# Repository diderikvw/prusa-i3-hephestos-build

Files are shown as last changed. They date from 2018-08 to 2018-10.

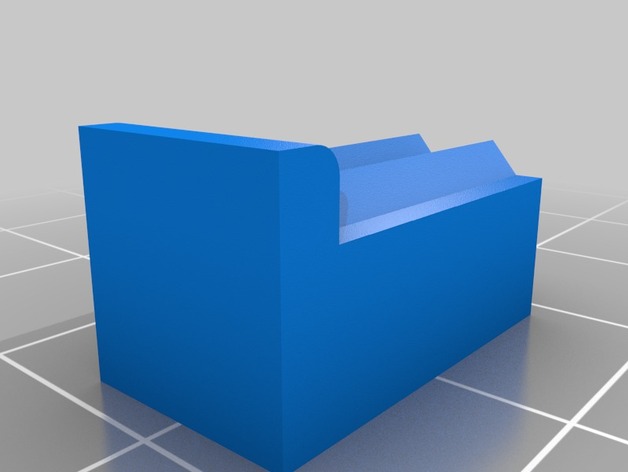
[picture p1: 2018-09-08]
3D Printable Parts/Thingiverse/By pixelmagic (thing 1411994)/images/da518802a75f78a3230417619e0c3546_preview_featured.jpg

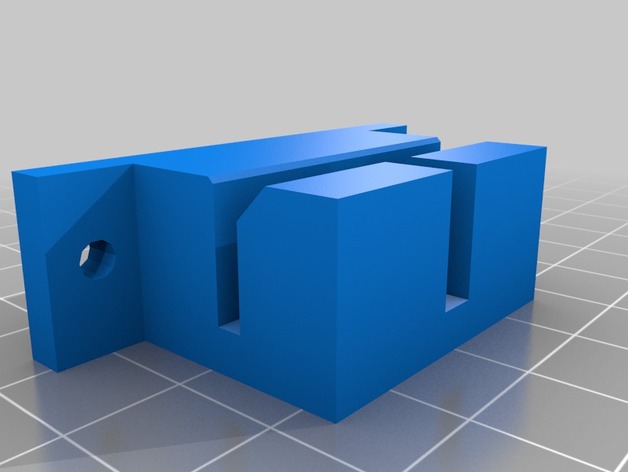
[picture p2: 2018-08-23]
3D Printable Parts/Thingiverse/By bqLabs (thing 371842)/images/EjeY_sujeta_correa_preview_featured.jpg

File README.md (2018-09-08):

# prusa-i3-hephestos-build
Repo to store stuff while building the 3D Printer Prusa i3 Hephestos

Information:
https://reprap.org/wiki/Prusa_i3_Hephestos

3D Printable parts:
Original Spanish: https://www.thingiverse.com/thing:371842
PLA
Infill 20%
0.1mm

English STL only: https://www.thingiverse.com/thing:1411994/

https://github.com/bq/prusa-i3-hephestos/tree/master/stl

https://www.bq.com/en/support/prusa/support-sheet

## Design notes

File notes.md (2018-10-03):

# Notes

## BOM

### Smooth rods
8mm
2 x 37 cm
2 x 34 cm
2 x 32 cm
total: 206 cm

reprapworld.nl 3 x 100 cm = EUR 12
aliexpress more expensive

### Flexible coupling
2x 5/5mm

reprapworld EUR 4 a piece = EUR 8
aliexpress EUR 1 a piece + EUR 4 shipping 12-15 days = EUR 5

### axial ball bearing B623ZZ
2x

reprapworld EUR 0,75 a piece

### GT2 pulley
20 teeth
diameter?
2x

reprapworld EUR 4 a piece = EUR 8
aliexpress EUR 0,50 + EUR 4 schipping 12-15 days = EUR 5

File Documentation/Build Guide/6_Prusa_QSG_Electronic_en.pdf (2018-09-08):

6

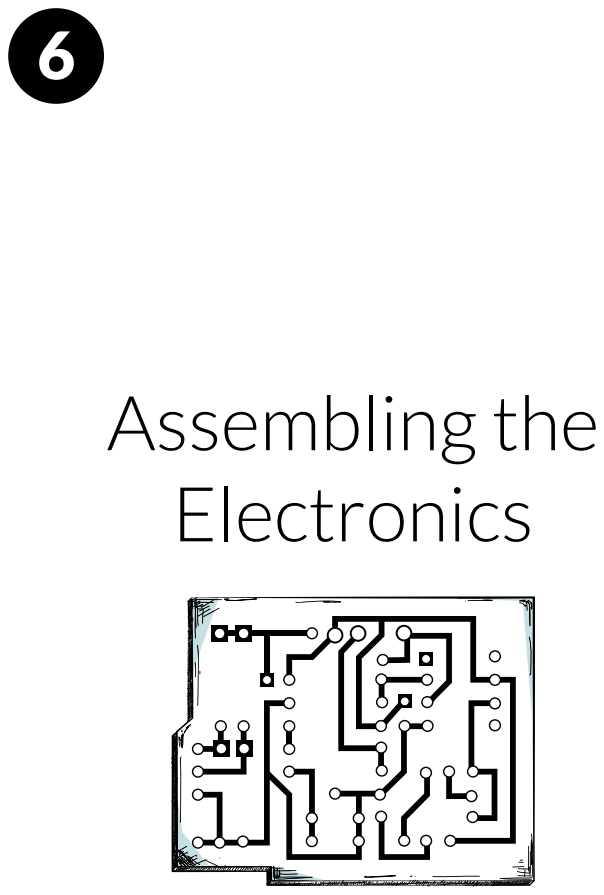
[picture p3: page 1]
Assembling the Electronics

### 1 x Ramps 1.4 (with 4 x Stepstick Drivers A4988 mounted) 3 x End-stop 1 x LCD Control Panel 1 x USB cable, type B, 1.8 metres 4 x Cable motor Nema 17 2 x Cable end-stop 40 cm 1 x Cable end-stop 85 cm 4 x Motor Nema 17 1 x Kit of cables for the extruder: Four-strand cable for Nema

17 bipolar step motor (2.5A 1.8 deg/step) with connector JST XHP-6 and 4-pin female connector + two-strand cable for thermistor of the extruder with 2-pin female connector
+ Cable for fan clamped to with nipple terminal + Cable blower clamped to with nipple terminal + Cable for cartridge heater clamped to with nipple terminal.

### 1 x Cable prepared for power supply (150 mm of flexible, two-

strand, bicolour cable with cross section of 1.5 mm² + Jack Adapter/ connector)

1 x 220 AC 12 DC 100W power supply 1 x Power supply/Network cable 1 x LCD Hinge printed part 1 x Ramp Bracket printed part 4 x Screw M3 x 10 - DIN-912 class 8.8 black 2 x Screw M3 x 12 - DIN-912 class 8.8 black 2 x Screw M3 x 16 - DIN-912 class 8.8 black 4 x Screw M3 x 20 - DIN-912 class 8.8 black 2 x Nut M3 - DIN 934 class 8 black 1 x Thermo-retractable tube of Ø2.5 x 500 mm 11 x Black strap 100 x 2.5 mm 1 x Fan 50 x 50 mm 2 x Igus Cable-carrier chain (25 and 27 links)

# List of components for the Electronics

1

# Installing the RAMPS 1.4

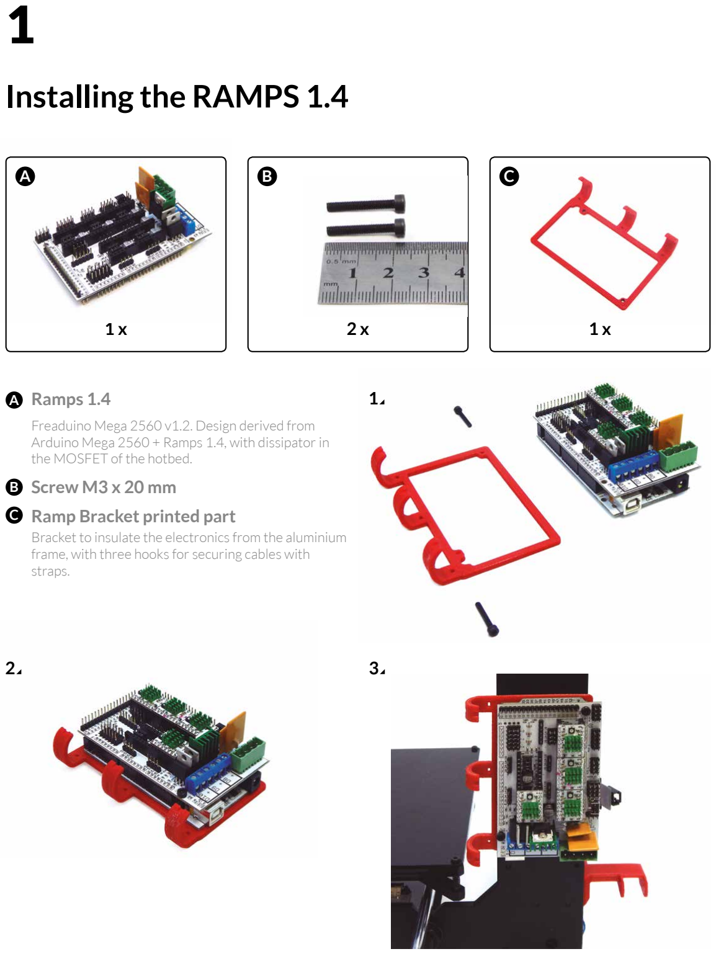
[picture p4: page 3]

1 x | 2 x | 1 x

Ramps 1.4

Freaduino Mega 2560 v1.2. Design derived from Arduino Mega 2560 + Ramps 1.4, with dissipator in the MOSFET of the hotbed.
Screw M3 x 20 mm
Ramp Bracket printed part
Bracket to insulate the electronics from the aluminium frame, with three hooks for securing cables with straps.
A | B | C

A

B

C

1

2 3

2

# Preparing the LCD control panel

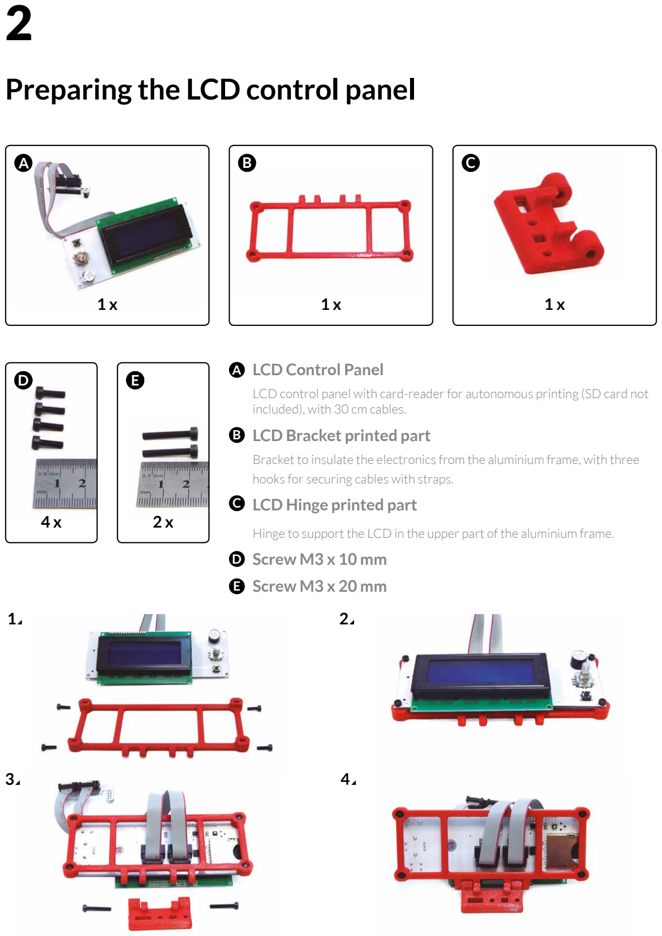
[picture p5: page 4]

1

### 1 x

LCD Control Panel

LCD control panel with card-reader for autonomous printing (SD card not included), with 30 cm cables.
LCD Bracket printed part

Bracket to insulate the electronics from the aluminium frame, with three hooks for securing cables with straps.
LCD Hinge printed part

Hinge to support the LCD in the upper part of the aluminium frame.
Screw M3 x 10 mm
Screw M3 x 20 mm

C

5

A

B

C

E

D

### 4 x

1 x | 1 x

D

B

15

### 2 x

E

A

1 2

3

3

# Mounting the LCD control panel onto the frame

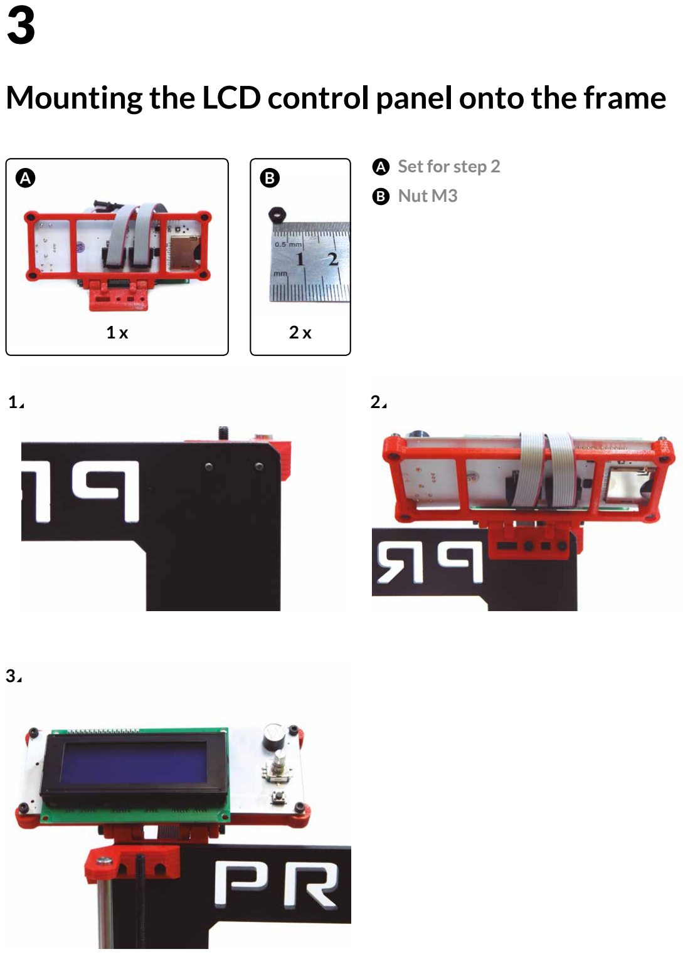
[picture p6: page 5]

### 2 x

Set for step 2
Nut M3

A B

A

B

### 1 x

1 2

3

4

# Putting the cables in the chains of Axle X and Axle Z

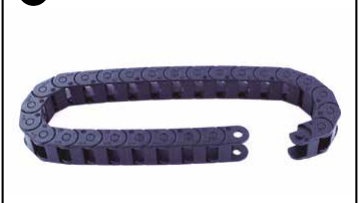
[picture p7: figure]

### 1 x

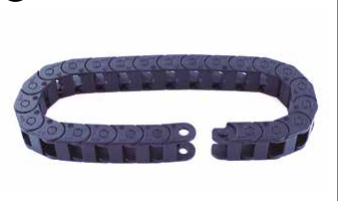
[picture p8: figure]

25-link Chain
Igus 045.10.018 Cable-carrier chain (external dimensions 15 x 10 mm)
27-link Chain
Igus 045.10.018 Cable-carrier chain (external dimensions 15 x 10 mm)
Kit of cables for extruder

C Cable for axial blower
D Cable for axial fan
E Cable for cartridge heater
F Nema motor cable
G Thermistor extruder cable

A B

A

B

### 1 x

### Assembly:

First, insert the cables into the 25-link chain of Axle X (2 and 3). Then insert them into the 27-link chain of Axle Z (4).

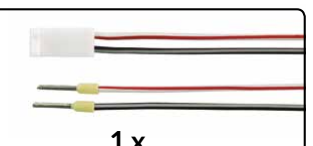
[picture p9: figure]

### 1 x

### 1 x

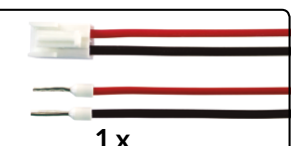
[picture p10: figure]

### 1 x

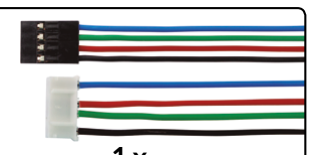
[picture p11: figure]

### 1 x

### 1 x

C

D

E

F

G

3

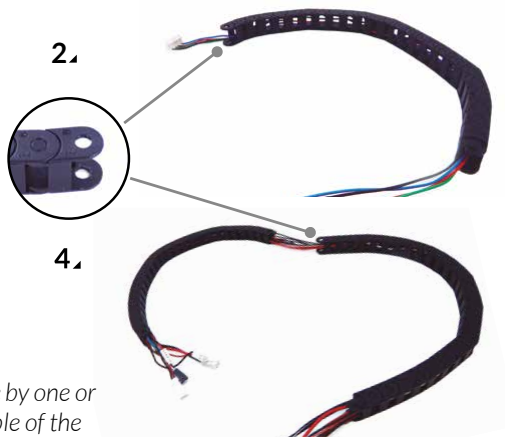
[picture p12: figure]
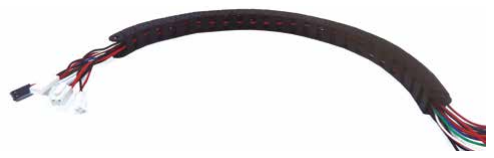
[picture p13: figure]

To make the task easier, insert the cables one by one or wrap them with adhesive tape. Insert the cable of the extruder motor first.

5

# Fitting the chain of Axle X

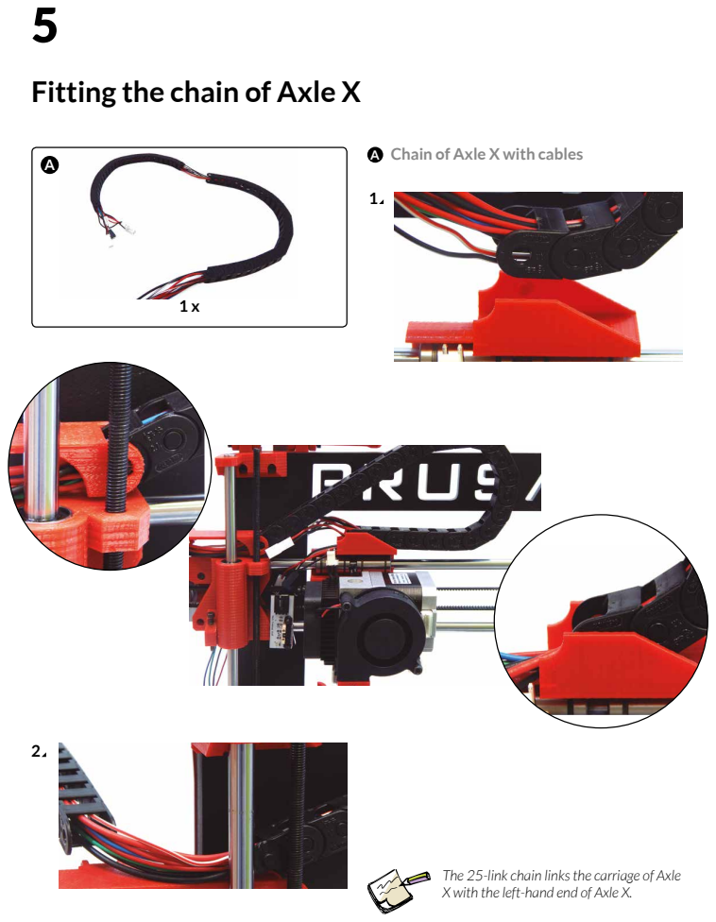
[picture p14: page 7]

Chain of Axle X with cables

The 25-link chain links the carriage of Axle
X with the left-hand end of Axle X.

6

# Inserting the cables of Axle Z and fitting the

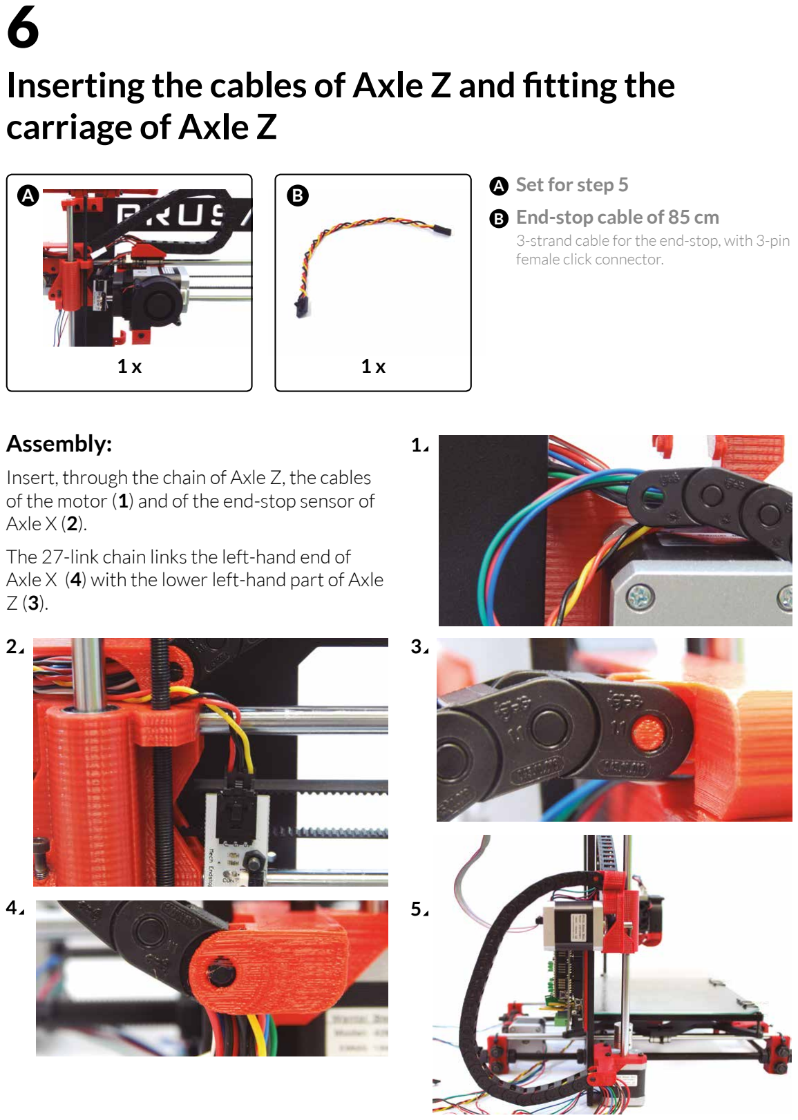
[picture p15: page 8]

# carriage of Axle Z

### Assembly:

Insert, through the chain of Axle Z, the cables of the motor (1) and of the end-stop sensor of Axle X (2).
The 27-link chain links the left-hand end of Axle X (4) with the lower left-hand part of Axle Z (3).

### 1 x

Set for step 5
End-stop cable of 85 cm
3-strand cable for the end-stop, with 3-pin female click connector.
A | B | A

### 1 x

B

1

2 3

5

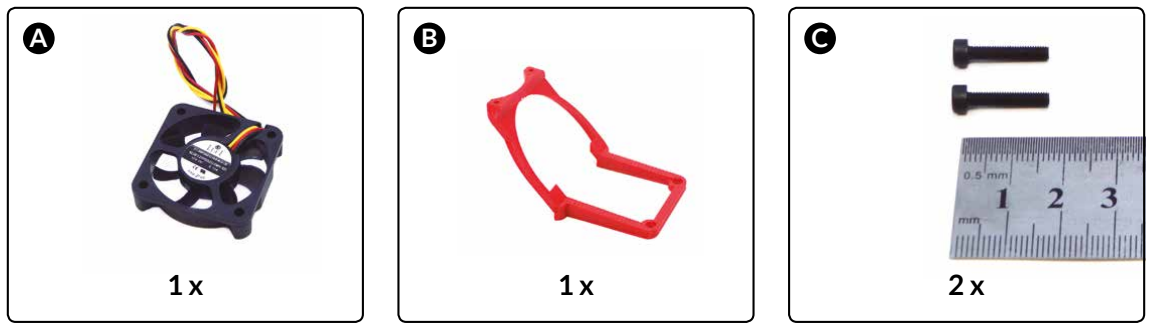
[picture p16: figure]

Fan 50 x 50 mm

12V DC 0.13A.
Fan support printed part

Support for the 50 x 50 mm fan, positioned above the electronics for correct cooling.
Screw M3 x 16 mm

A

B

C

7

# Preparing the fan

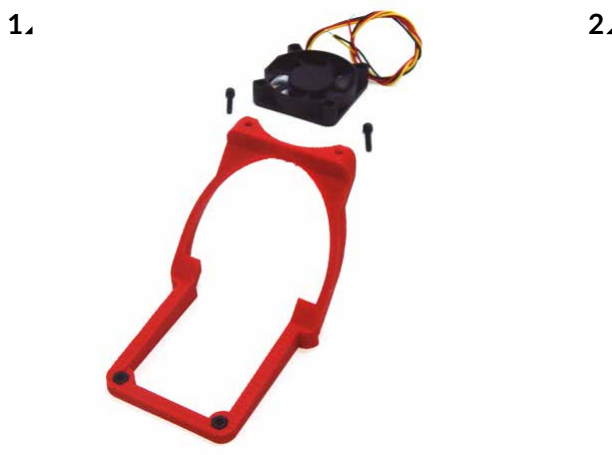
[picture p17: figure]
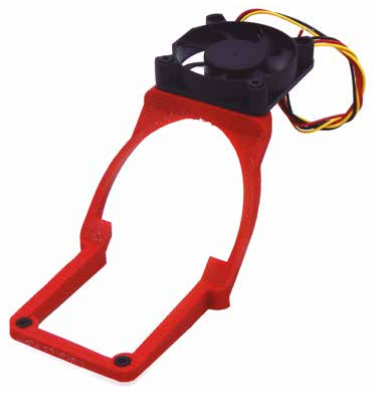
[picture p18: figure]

8

# Connecting and guiding the cables

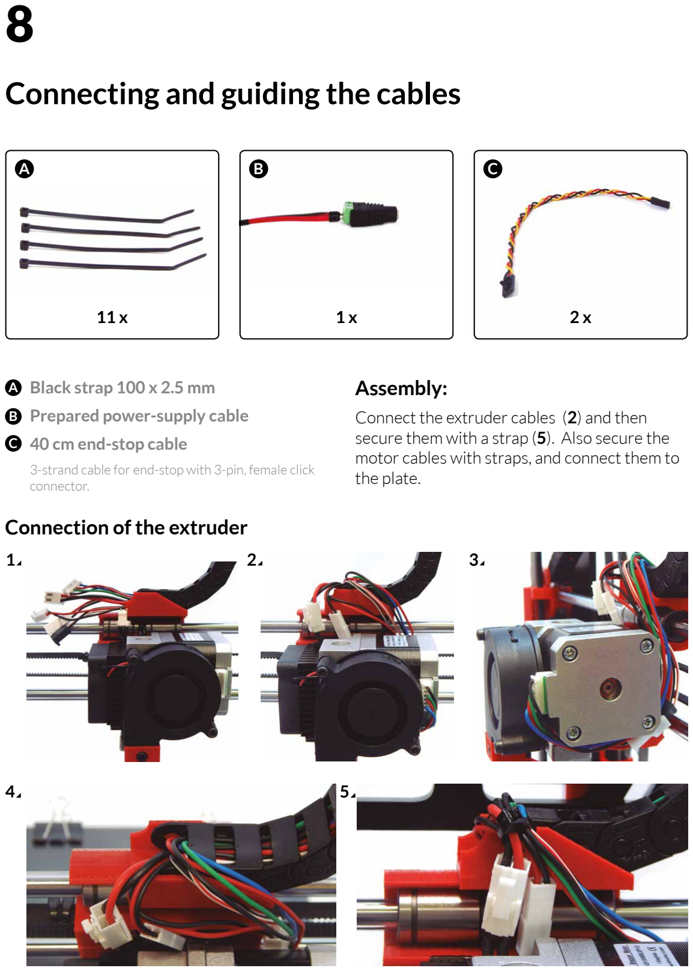
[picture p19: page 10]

### 1 x

A B

11 x | 2 x

C

Black strap 100 x 2.5 mm
Prepared power-supply cable

### 40 cm end-stop cable

3-strand cable for end-stop with 3-pin, female click connector.

A

B

C

### Connection of the extruder

### Assembly:

Connect the extruder cables (2) and then secure them with a strap (5). Also secure the motor cables with straps, and connect them to the plate.

1 | 2 | 3

4 5

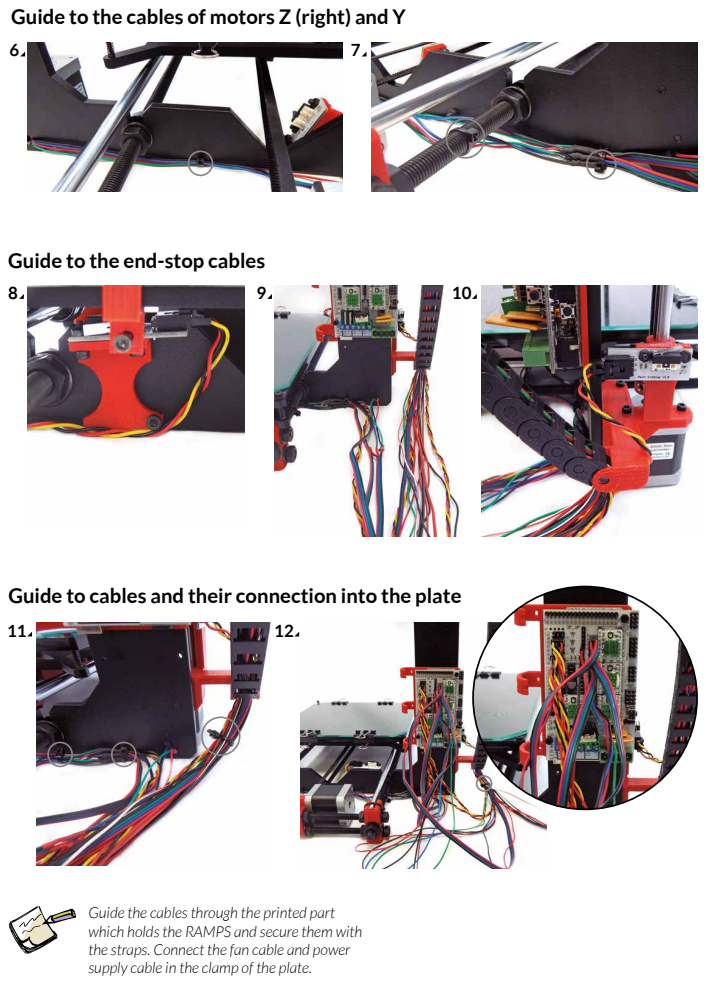
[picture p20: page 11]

Guide to the cables of motors Z (right) and Y

Guide to the end-stop cables

Guide to cables and their connection into the plate

Guide the cables through the printed part
which holds the RAMPS and secure them with
the straps. Connect the fan cable and power
supply cable in the clamp of the plate.

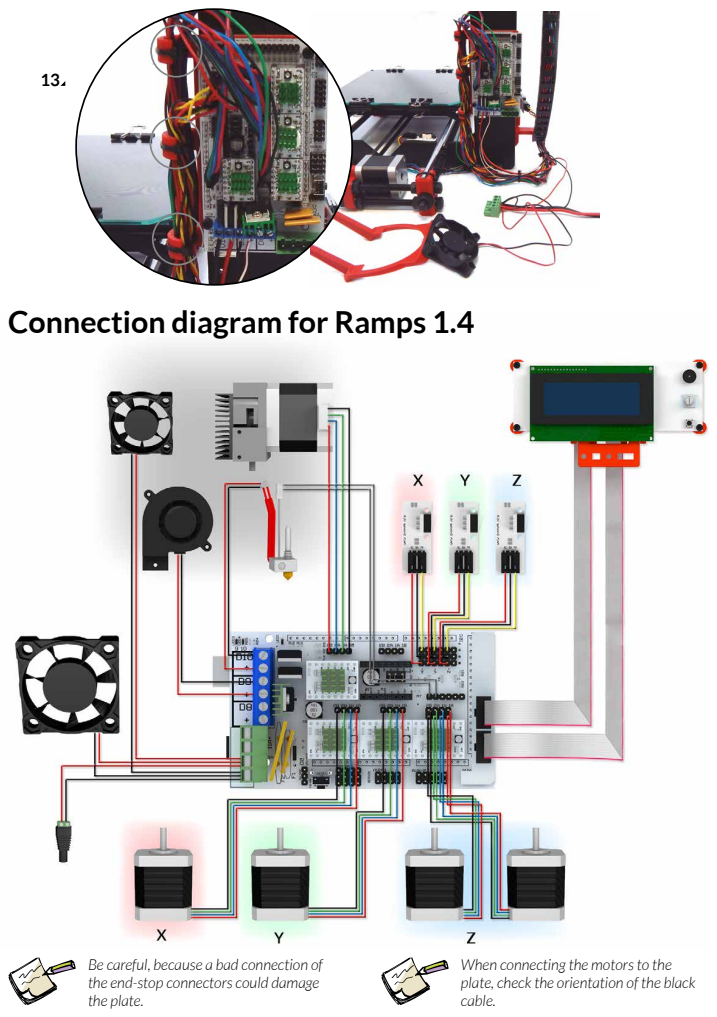
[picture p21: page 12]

Connection diagram for Ramps 1.4

Be careful, because a bad connection of
the end-stop connectors could damage
the plate.

When connecting the motors to the
plate, check the orientation of the black
cable.

9

# Fitting the fan

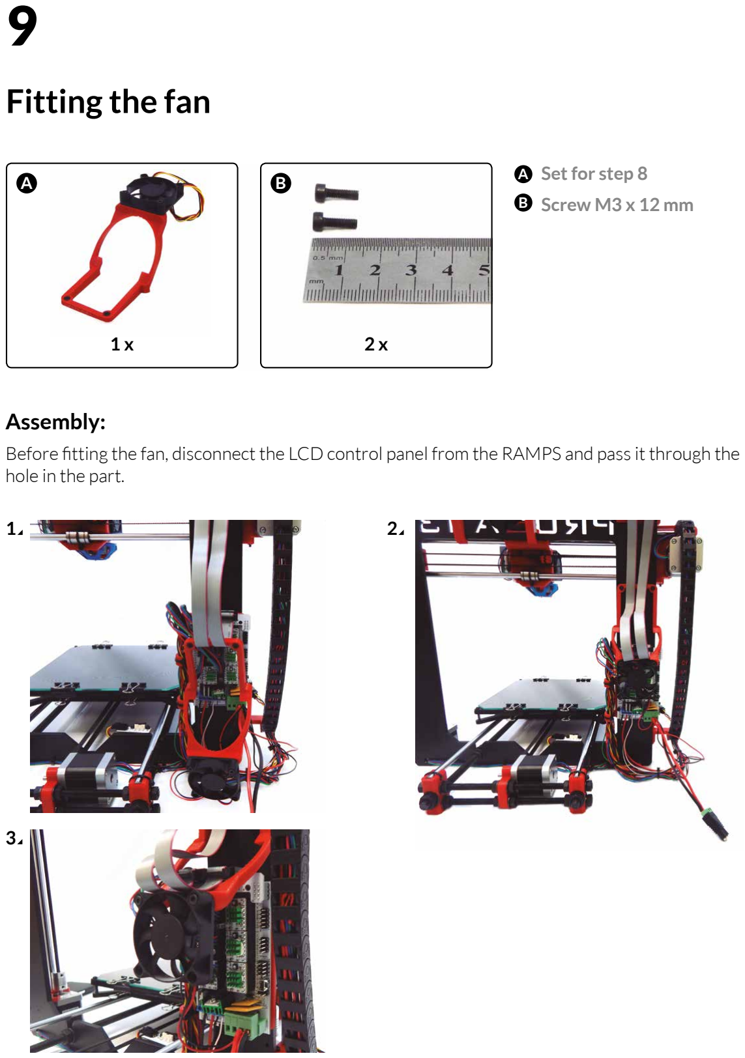
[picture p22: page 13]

### 2 x

A B

### 1 x

Set for step 8
Screw M3 x 12 mm

A
B

### Assembly:

Before fitting the fan, disconnect the LCD control panel from the RAMPS and pass it through the hole in the part.

1 2

3

10

# Fitting of the support for the spool of filament

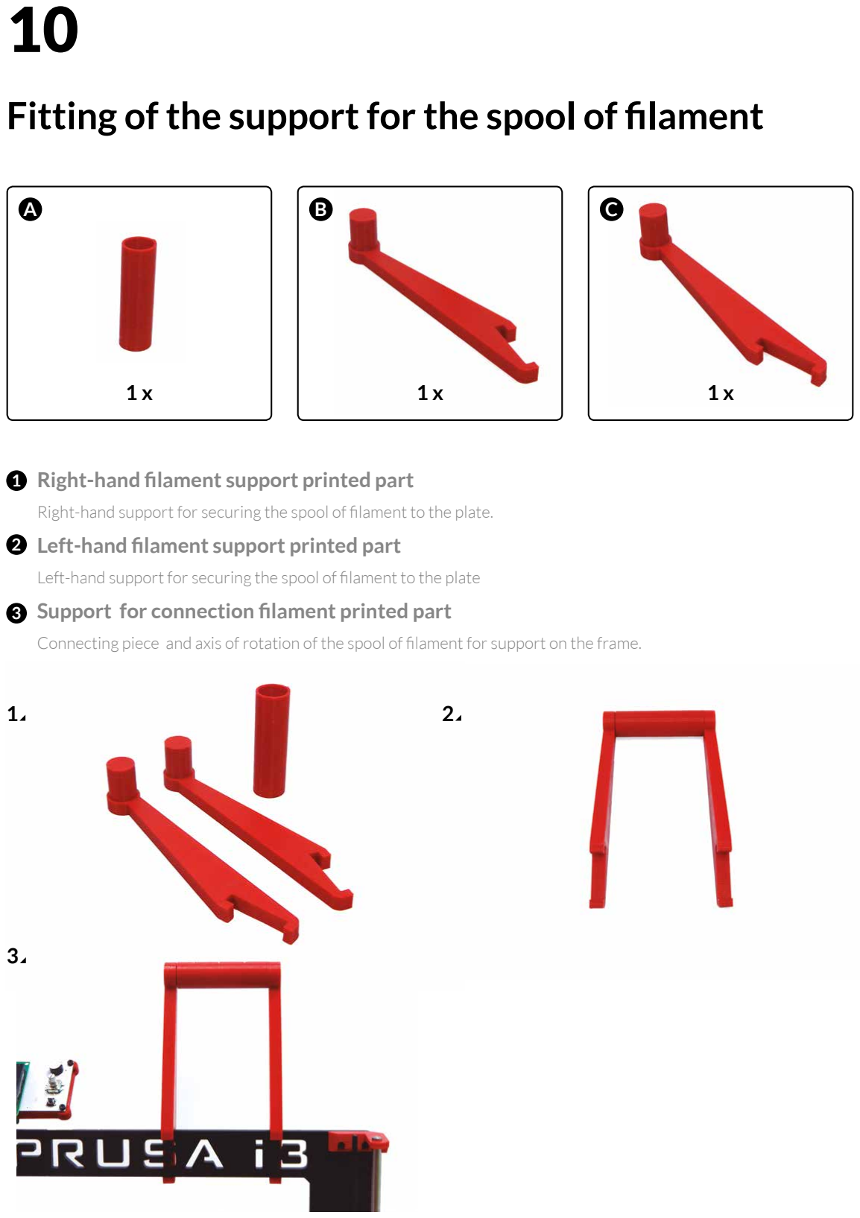
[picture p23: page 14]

### 1 x

A B

1 x | 1 x

C

Right-hand filament support printed part

Right-hand support for securing the spool of filament to the plate.
Left-hand filament support printed part

Left-hand support for securing the spool of filament to the plate
Support for connection filament printed part

Connecting piece and axis of rotation of the spool of filament for support on the frame.

1

2

3

1 2

3

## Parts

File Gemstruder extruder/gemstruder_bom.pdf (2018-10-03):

## Gemstruder Bill of Materials

Part | Amount per kit
Gemstruder body | 1
Gemstruder bolt gear | 1
Gemstruder stepper gear | 1
Gemstruder idler | 1
Gemstruder idler crossbar | 1
Gemstruder tension handle | 1
Gemstruder gear spacer ring | 3
Black hobbed bolt | 1
M8 lock nut | 1
Pneumatic fitting | 1
608ZZ bearing | 3
8x16mm idler insert | 1
M4 lock nut | 4
M4 x 50mm bolt | 2
M4 spring washer | 4
M4 washer | 6
M3 x 8mm bolt | 3
M3 x 25mm bolt | 1
Grub screw | 1

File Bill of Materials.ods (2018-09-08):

Prusa i3 Hephestos 3D Printer Build
Diderik van Wingerden
Bill of Materials
https://reprap.org/wiki/Prusa_i3_Hephestos#Bill_of_Materials
Tools
 | Name (English) | Name (Dutch) | Quantity | Description
 | Allen key s/long Ø 2 UNIOR Ø 2 mm | Imbus sleutel | 1
 | Allen key s/long Ø 2.5 mm | Imbus sleutel | 1
 | Ceramic screw driver trimmer for electronics. |  | 1 | Screwdriver for adjusting the current of the motor drivers step by step, bipolar Nema 17 and extruder.
 | Precision needle 0.4 mm diameter |  | 2 | Required for maintaining the Hotend and removing blockages.
 | Printed spanner 10 (M6) - 13 (M8) - 17 (M10) | Printed spanner for nuts M6, M8 & M10 (corresponds to spanner size 10, 13, & 17) | 1
Electronics
 | Ramps 1.4 |  | 1 | Freaduino Mega 2560 v1.2. Design based on Arduino Mega 2560 + Ramps 1.4, with heatsink on the MOSFET of the hot bed.
 | Stepstick Drivers A4988 |  | 4 | Stepstick Drivers A4988 with 4 layers and improved heat dissipation to avoid overheating & heatsinks for attached drivers.
 | Endstop |  | 3 | Endstop mounted on PCB with LED indicator.
 | LCD control panel |  | 1 | LCD control panel with card reader for automatic printing (SD card not included) and 30 cm cables.
 | USB cable (type B), 1.8 m |  | 1 | Standard USB cable with male connectors (type A & B) 1.8 meters long.
 | Motor wire Nema 17 |  | 4 | 4 strand cable for bipolar stepping motor Nema 17 (2.5A 1.8deg/step) with female connector.
 | Endstop wire 40 cm |  | 2 | 3 strand cable for Endstop with female click connector (3pins) 40 cm long.
 | Endstop wire 85 cm |  | 1 | 3 strand cable for Endstop with female click connector (3pins) 85 cm long.
 | Motor Nema 17 |  | 4 | Bipolar stepping motor Nema 17 (2.5A 1.8deg/step)
 | Wiring kit for extruder (Motor wire Nema (with connector) + Thermistor wire with connector + Fan and blower wire + Heater cartridge) |  | 1 | Wiring kit for extruder (4 strand cable for bipolar stepping motor Nema 17 (2.5A 1.8deg/step) with connector JST XHP-6 & female 4 pin connector + 2 strand cable for extruder thermistor with female 2 pin connector + Crimped fan and blower wire with terminal sleeve + Cartridge heater cable with terminal sleeve.
 | 150 mm of flexible wire with two bicolor strands with cross section of 1 mm² |  | 1
 | Power supply 220 AC 12 DC 100W |  | 1 | Power supply with 1.10m cable, 100 W with 2.1mm connector Jack INPUT: 100-240VAC 1,8A 50-60Hz & OUTPUT: 12 VDC 8.0A).
 | Power Supply Cable (European) |  | 1 | Cable of 1,10m for 220V AC with Schuko connector (Male) & IEC-60320-C13 connector (Female).
 | M3x10 Screw - DIN-912 Class 8.8 Black |  | 4
 | M3x12 Screw - DIN-912 Class 8.8 Black |  | 2

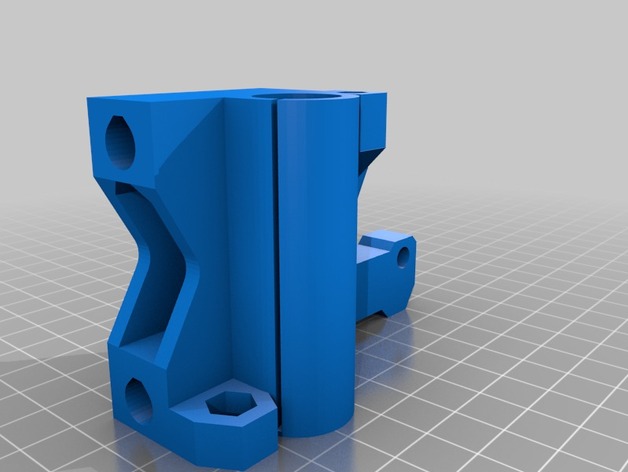
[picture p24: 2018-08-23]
3D Printable Parts/Thingiverse/By bqLabs (thing 371842)/images/EjeX_izquierda_preview_featured.jpg

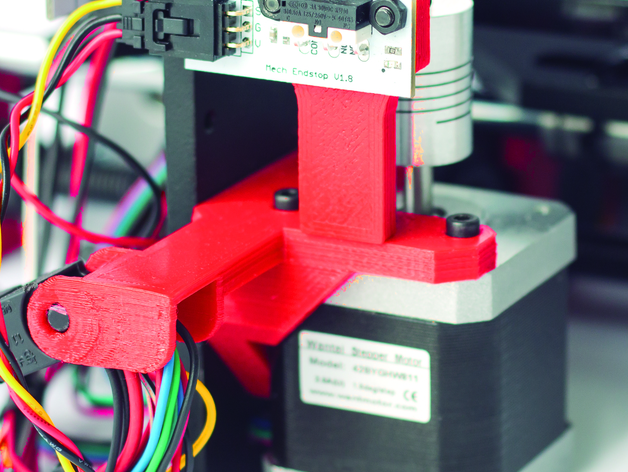
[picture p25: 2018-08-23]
3D Printable Parts/Thingiverse/By bqLabs (thing 371842)/images/IMG_0080_preview_featured.jpg

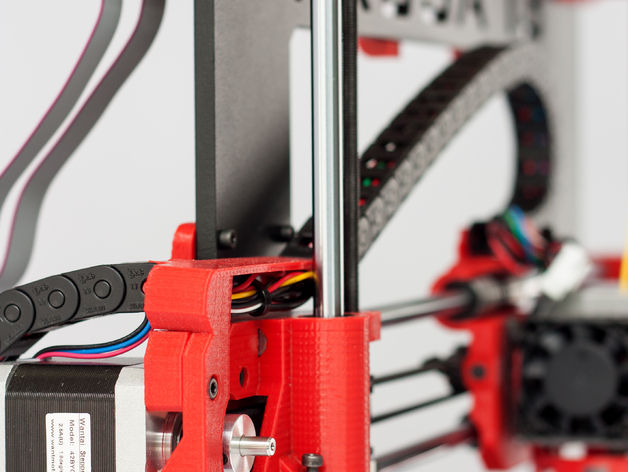
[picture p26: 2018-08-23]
3D Printable Parts/Thingiverse/By bqLabs (thing 371842)/images/IMG_0099_preview_featured.jpg

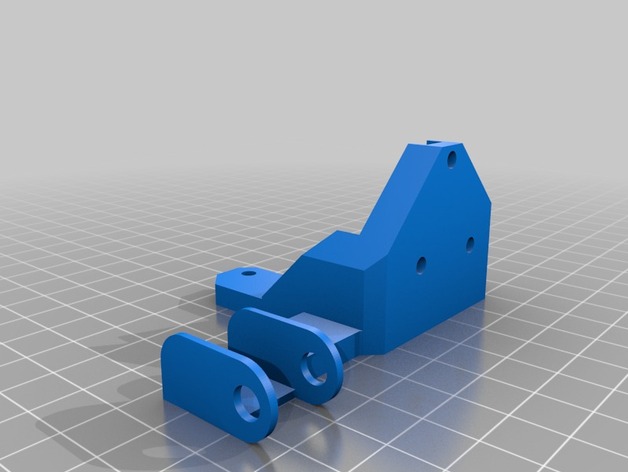
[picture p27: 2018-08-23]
3D Printable Parts/Thingiverse/By bqLabs (thing 371842)/images/EjeZ_soporte_inferior_izquierda_preview_featured.jpg

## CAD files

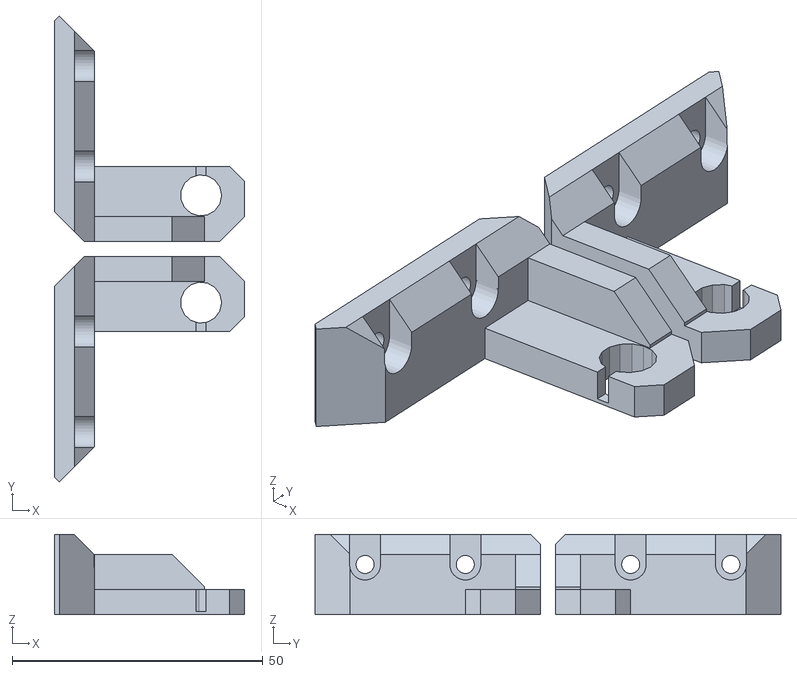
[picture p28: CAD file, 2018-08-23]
3D Printable Parts/Thingiverse/By bqLabs (thing 371842)/files/EjeZ_soporte_superior.stl
38.0 x 93.0 x 16.0

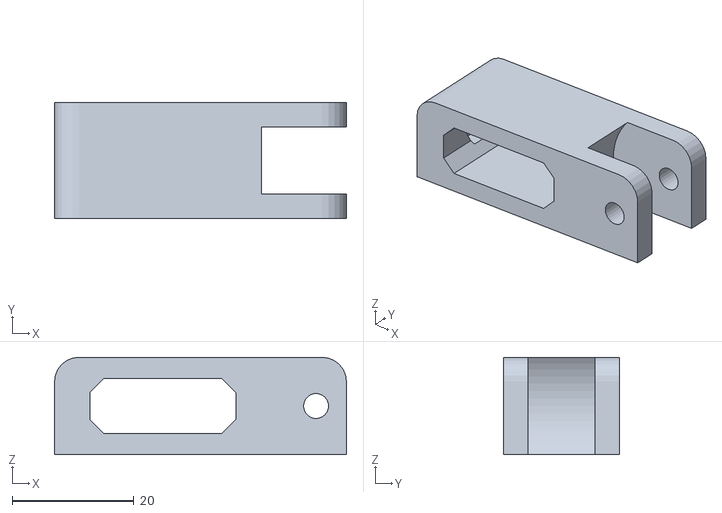
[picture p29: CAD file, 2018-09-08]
3D Printable Parts/Thingiverse/By pixelmagic (thing 1411994)/files/y-tensioner.stl
48.0 x 19.0 x 16.0

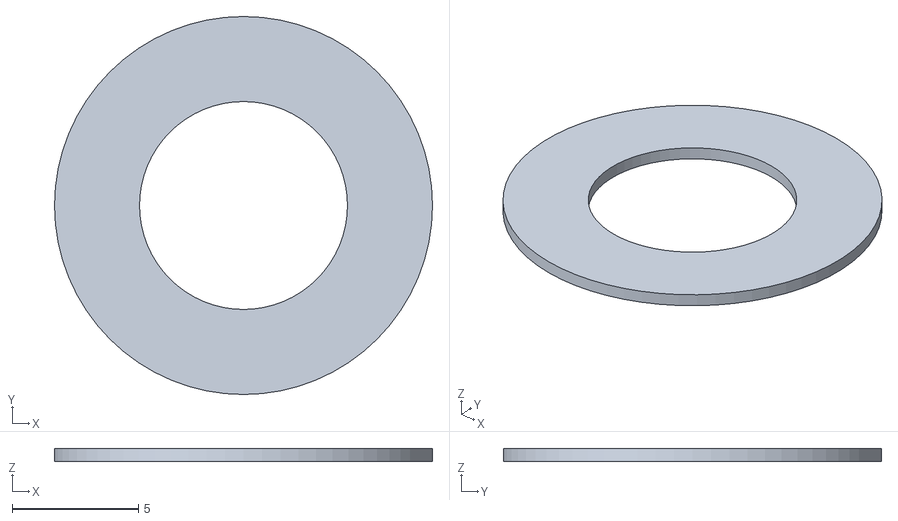
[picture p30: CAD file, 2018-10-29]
Gemstruder extruder/Gemstruder V1.0/Gemstruder - Spacer Ring - 0.5mm.stl
15.0 x 15.0 x 0.5

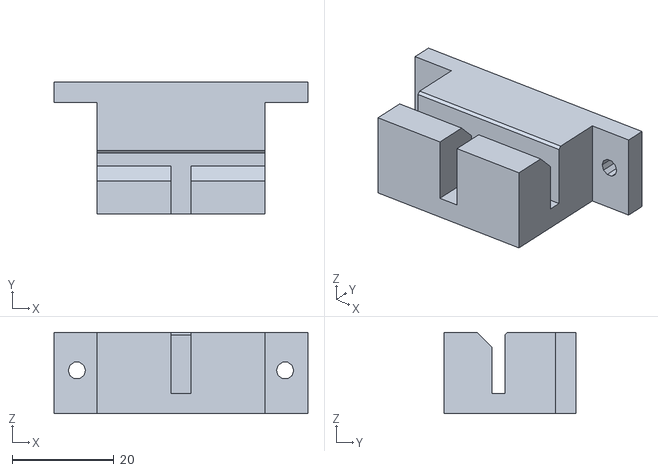
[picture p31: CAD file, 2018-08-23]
3D Printable Parts/Thingiverse/By bqLabs (thing 371842)/files/EjeY_sujeta_correa.stl
50.0 x 26.0 x 16.0

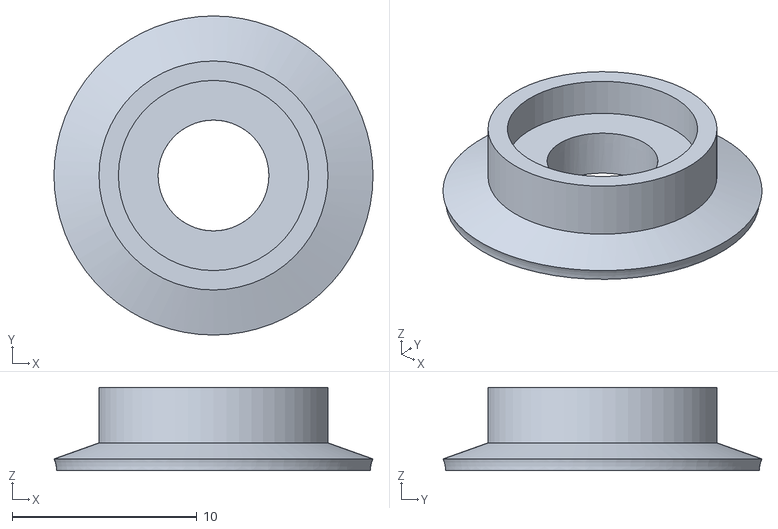
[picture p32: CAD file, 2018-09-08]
3D Printable Parts/Thingiverse/By pixelmagic (thing 1411994)/files/polea_V2.stl
17.3 x 17.3 x 4.50

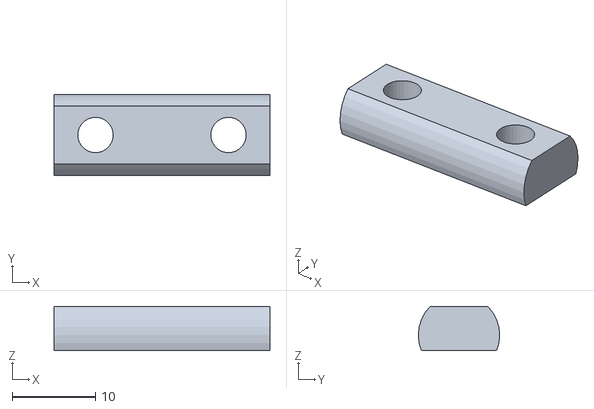
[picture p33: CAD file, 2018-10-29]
Gemstruder extruder/Gemstruder V1.0/Gemstruder - Idler Crossbar.stl
26.0 x 9.80 x 5.34

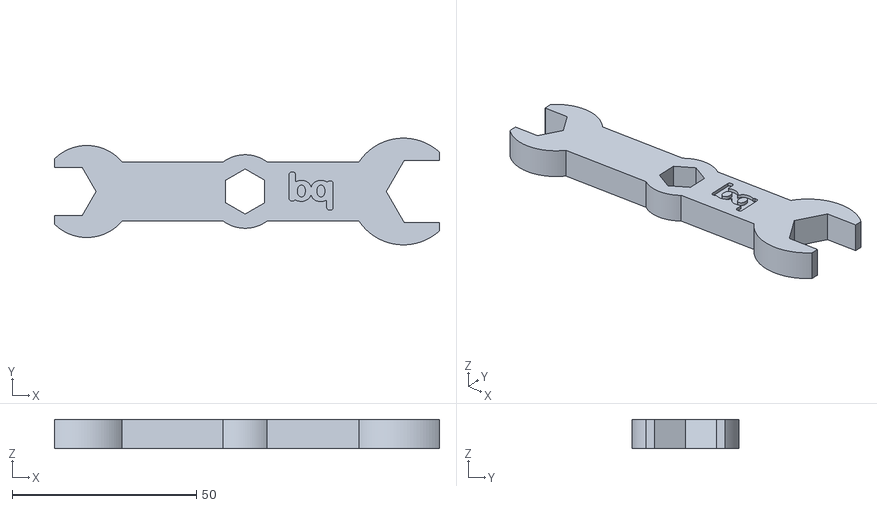
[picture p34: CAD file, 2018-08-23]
3D Printable Parts/Thingiverse/By bqLabs (thing 371842)/files/llave_10-M6_13-M8_17-M10_bq.stl
104.6 x 29.0 x 8.00

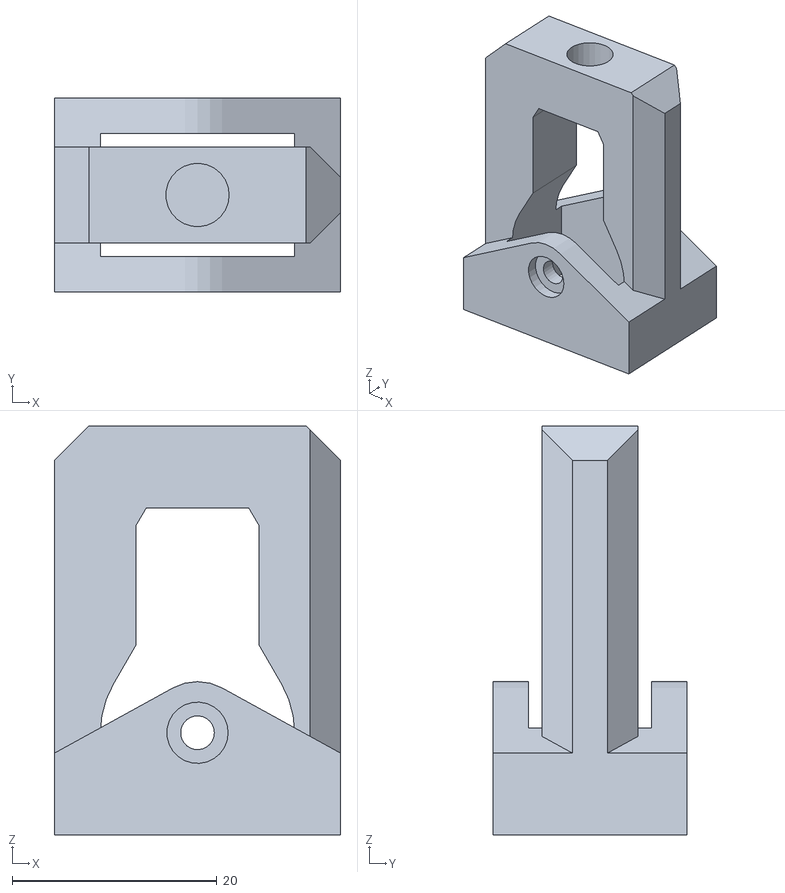
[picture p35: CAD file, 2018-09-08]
3D Printable Parts/Thingiverse/By pixelmagic (thing 1411994)/files/x-axis-belt-tensioner.stl
28.0 x 19.0 x 40.0

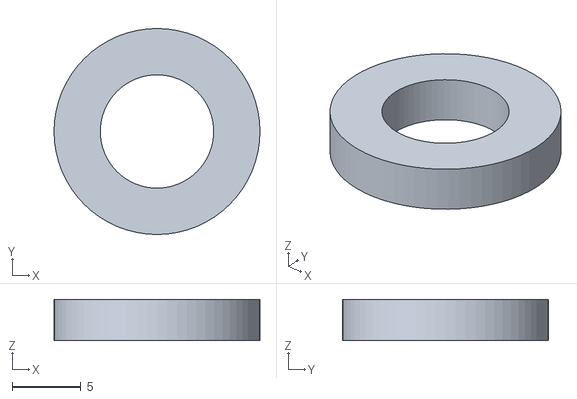
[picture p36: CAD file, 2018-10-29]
Gemstruder extruder/Gemstruder V1.0/Gemstruder - Spacer Ring - 3mm.stl
15.0 x 15.0 x 3.00

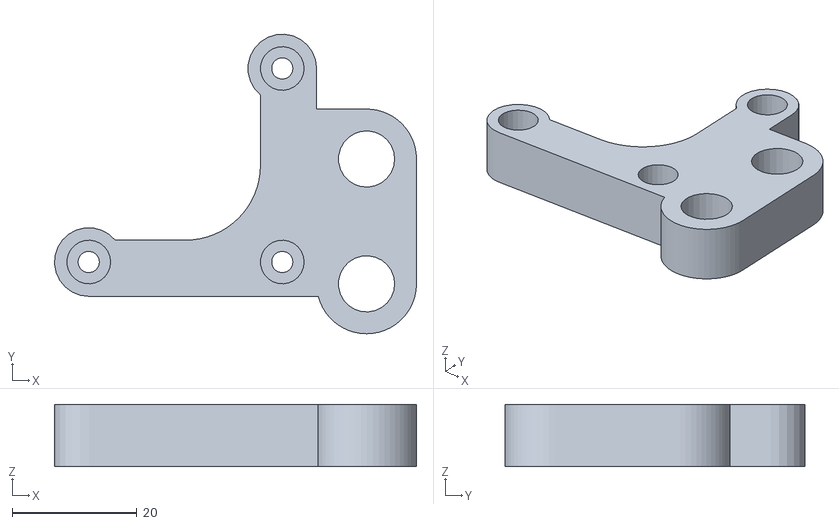
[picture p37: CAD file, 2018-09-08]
3D Printable Parts/Thingiverse/By pixelmagic (thing 1411994)/files/y-motor.stl
58.0 x 48.0 x 10.0

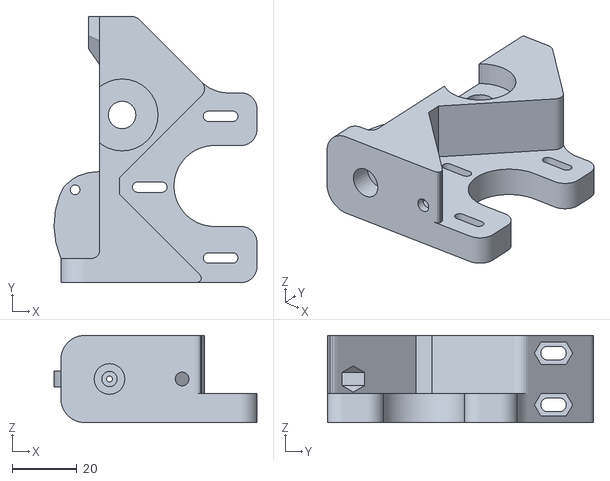
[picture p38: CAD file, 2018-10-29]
Gemstruder extruder/Gemstruder V1.0/Gemstruder - Body.stl
62.8 x 82.4 x 27.0

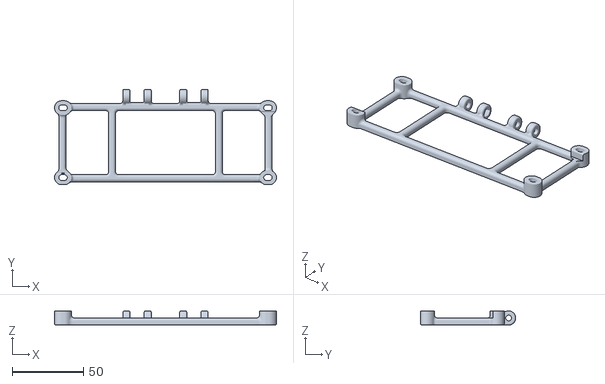
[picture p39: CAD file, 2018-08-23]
3D Printable Parts/Thingiverse/By bqLabs (thing 371842)/files/Soporte_lcd.stl
156.0 x 67.0 x 10.0

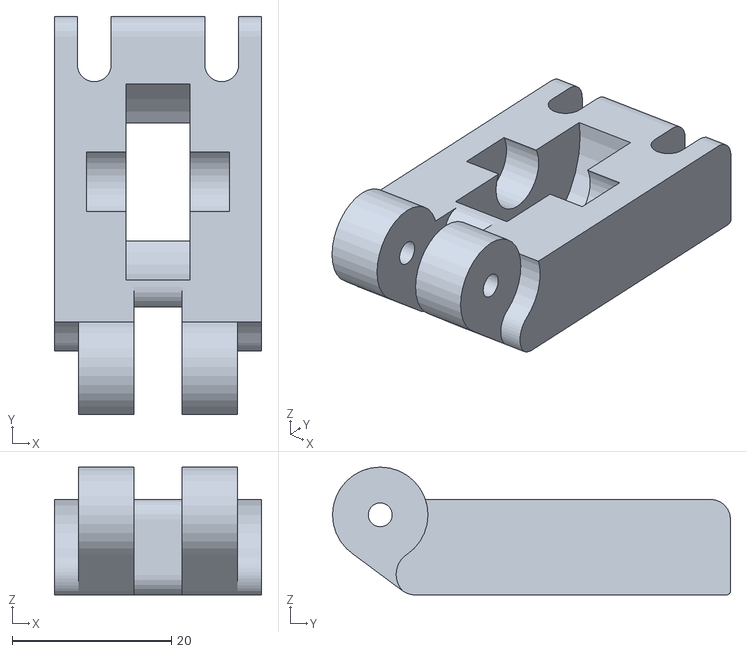
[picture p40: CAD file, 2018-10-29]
Gemstruder extruder/Gemstruder V1.0/Gemstruder - Idler.stl
26.0 x 50.0 x 16.1

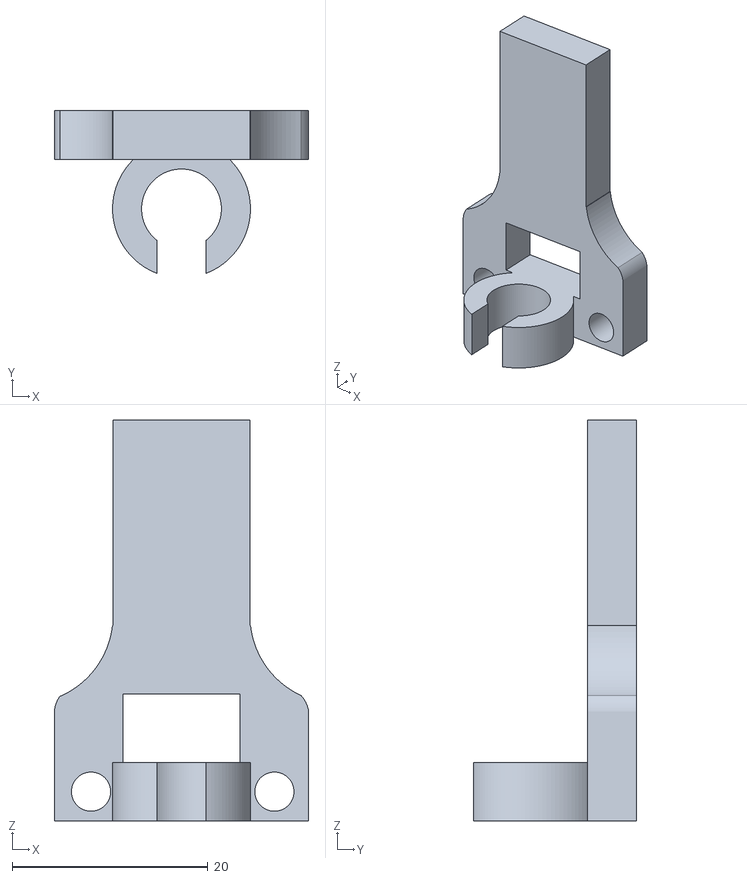
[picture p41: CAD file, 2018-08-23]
3D Printable Parts/Thingiverse/By bqLabs (thing 371842)/files/EjeZ_final_carrera.stl
26.0 x 16.6 x 41.0

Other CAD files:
3D Printable Parts/Thingiverse/By bqLabs (thing 371842)/files/EjeY_tensor_rodamientoB623ZZ.stl.stl
3D Printable Parts/Thingiverse/By pixelmagic (thing 1411994)/files/EjeY_motorV2.stl
3D Printable Parts/Thingiverse/By pixelmagic (thing 1411994)/files/reel-holder-right-support.stl
Gemstruder extruder/Gemstruder V1.0/Gemstruder - Spacer Ring - 1mm.stl
3D Printable Parts/Thingiverse/By bqLabs (thing 371842)/files/carroX_con_cadeneta.SCAD
3D Printable Parts/Thingiverse/By bqLabs (thing 371842)/files/Eje_X_acople_cadeneta_izquierda.scad
3D Printable Parts/Thingiverse/By bqLabs (thing 371842)/files/Eje_X_izquierda.scad
3D Printable Parts/Thingiverse/By bqLabs (thing 371842)/files/Eje_Z_final_carrera.scad
3D Printable Parts/Thingiverse/By bqLabs (thing 371842)/files/Bisagra_lcd.stl
3D Printable Parts/Thingiverse/By bqLabs (thing 371842)/files/EjeX_Polea_rodamientoB623ZZ.stl
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

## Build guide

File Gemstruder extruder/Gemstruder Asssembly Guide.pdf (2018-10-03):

Gemstock 3D | Gemstruder Assembly Guide

# Gemstruder

# assembly guide

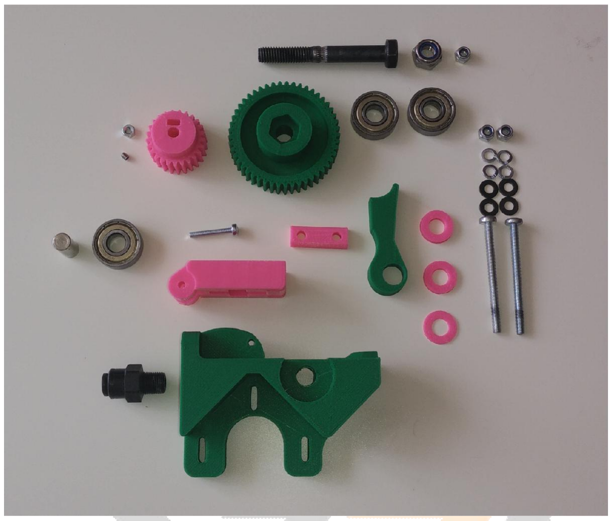
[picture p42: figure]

Gemstock 3D | Gemstruder Assembly Guide

With a printed Gemstruder body in hand and a fire in the heart, we traverse on the adventure that is building the Gemstruder.

Insert the 608ZZ bearings into the dedicated round holes on both sides of the body. Make sure they are as flush as they can against the inside.

Then twist the pneumatic fitting into the front of the body. Beware that it might not go in all the way, do not overtighten it as it might strip the threads.

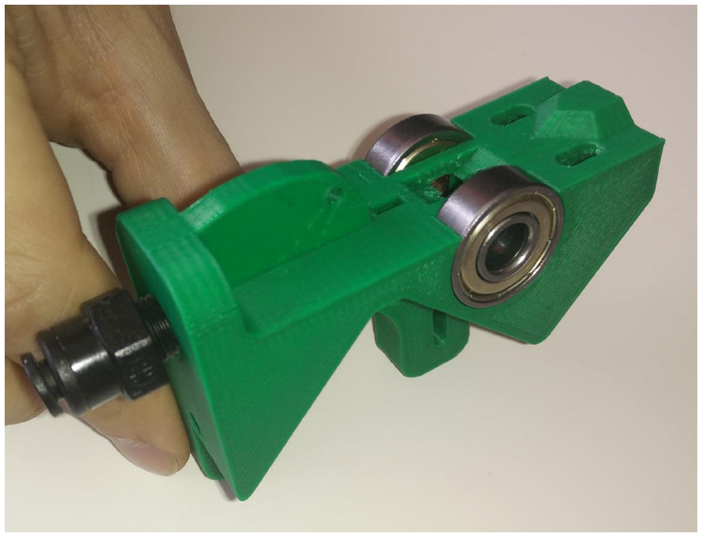
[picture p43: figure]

Gemstock 3D | Gemstruder Assembly Guide

Now add a M4 lock nut into the mounting hole into the inside of the body.

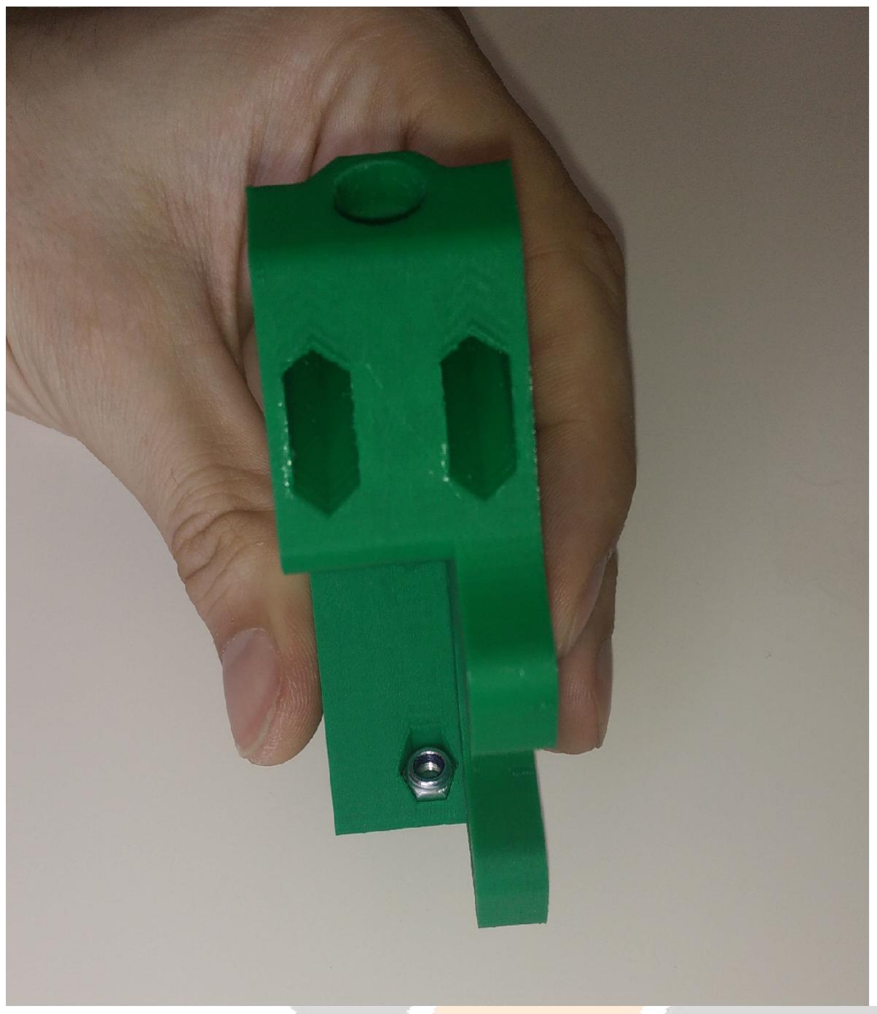
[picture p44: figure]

Gemstock 3D | Gemstruder Assembly Guide

Time to add the idler M4 lock nuts, if you can’t press them in then you can use a M4x50mm bolt to pull/push them into their sockets.

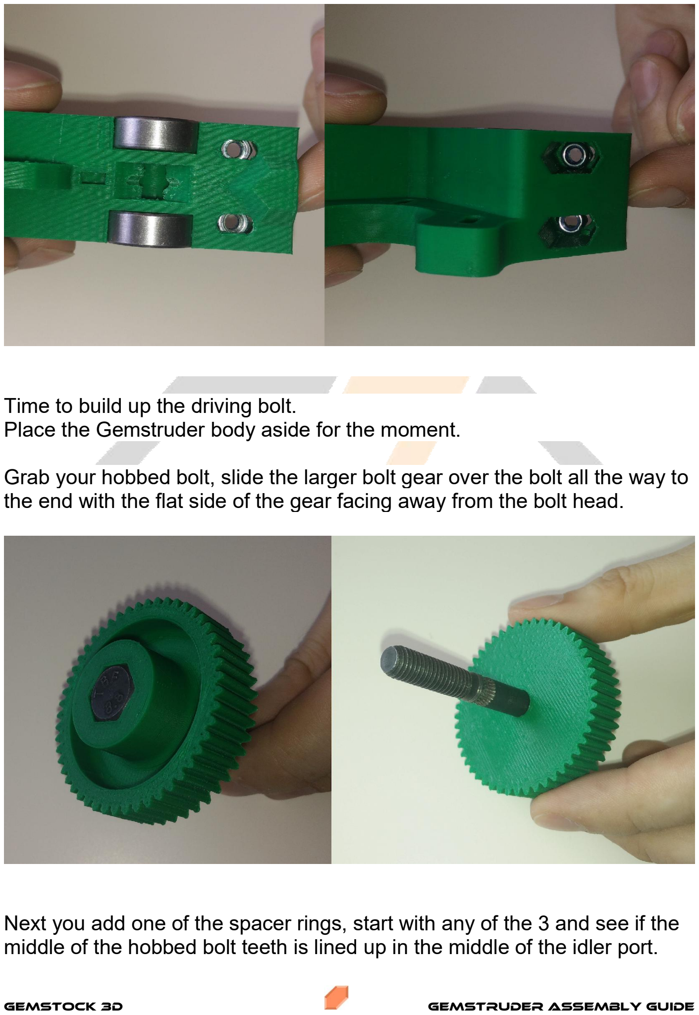
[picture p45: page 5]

Gemstock 3D | Gemstruder Assembly Guide

Time to build up the driving bolt.
Place the Gemstruder body aside for the moment.

Grab your hobbed bolt, slide the larger bolt gear over the bolt all the way to the end with the flat side of the gear facing away from the bolt head.

Next you add one of the spacer rings, start with any of the 3 and see if the middle of the hobbed bolt teeth is lined up in the middle of the idler port.

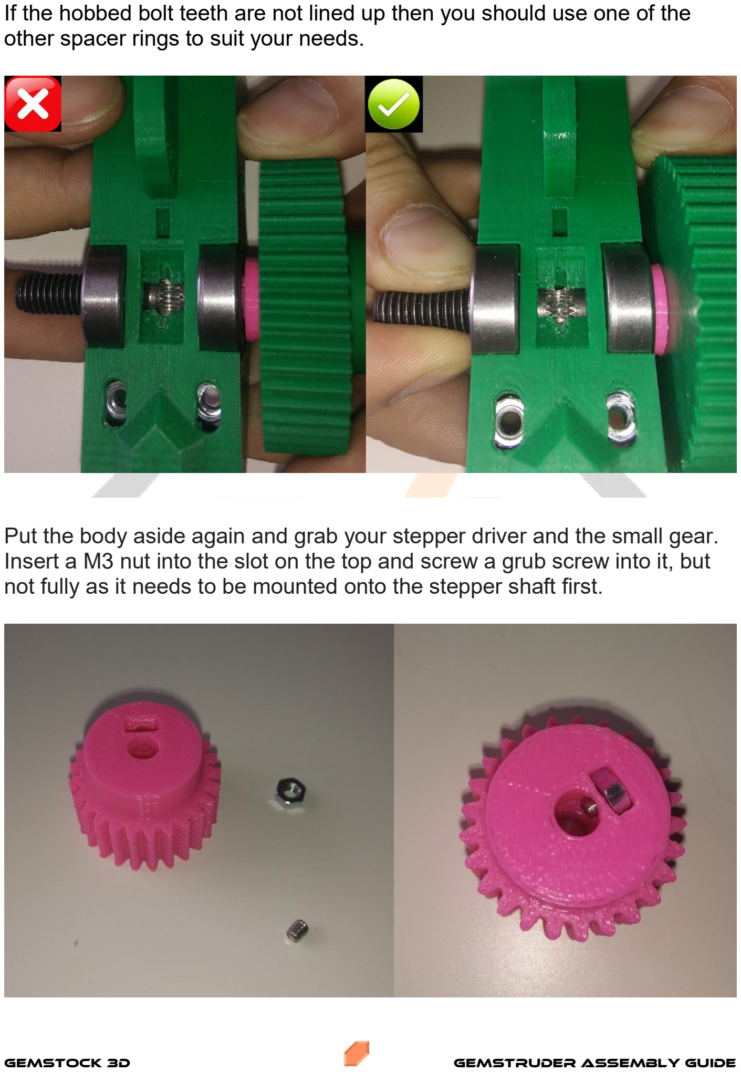
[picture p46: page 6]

Gemstock 3D | Gemstruder Assembly Guide

If the hobbed bolt teeth are not lined up then you should use one of the other spacer rings to suit your needs.

Put the body aside again and grab your stepper driver and the small gear. Insert a M3 nut into the slot on the top and screw a grub screw into it, but not fully as it needs to be mounted onto the stepper shaft first.

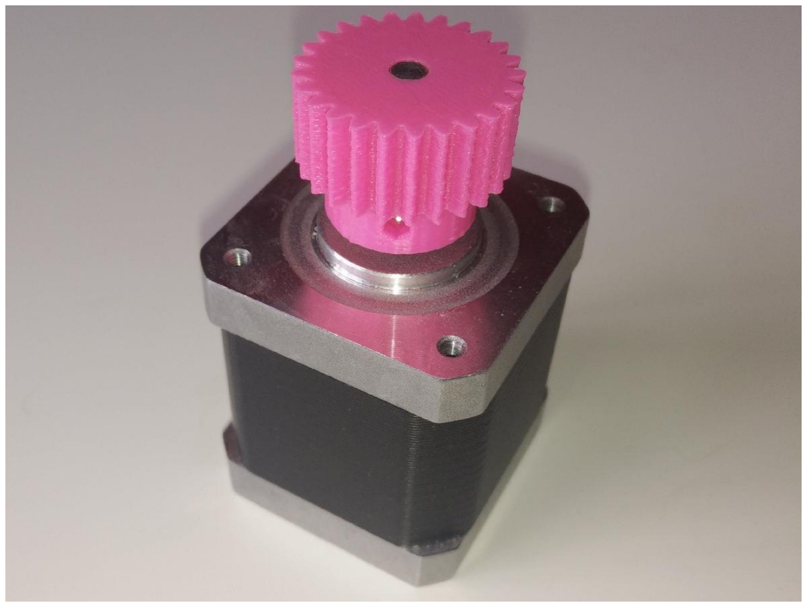
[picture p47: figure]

Gemstock 3D | Gemstruder Assembly Guide

Next put the small gear onto your stepper with the grub screw side towards the body of the stepper motor.
And if your stepper motor has a flat side on the shaft then line up the grub screw with the flat side.

Next hold the stepper in place on the body so the gears align, now adjust the height of the small gear on the stepper to make sure both gears align and have the best meshing of the teeth possible. Insert 2x M3x10mm bolts into the mounting holes and into the stepper and tighten these down whilst holding the gears in contact with each other.

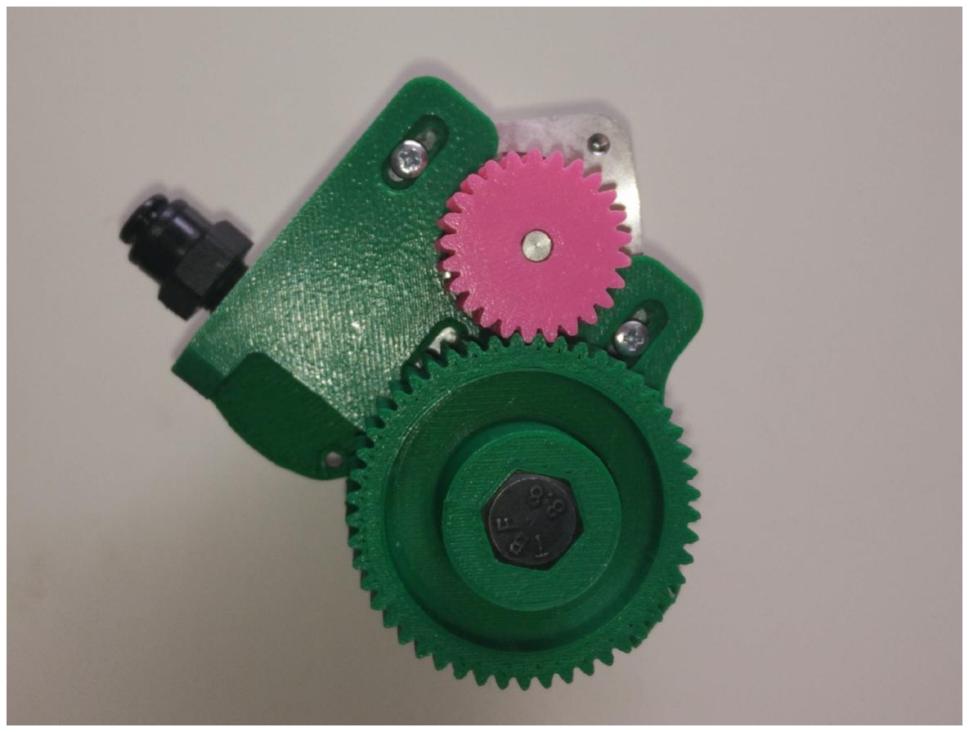
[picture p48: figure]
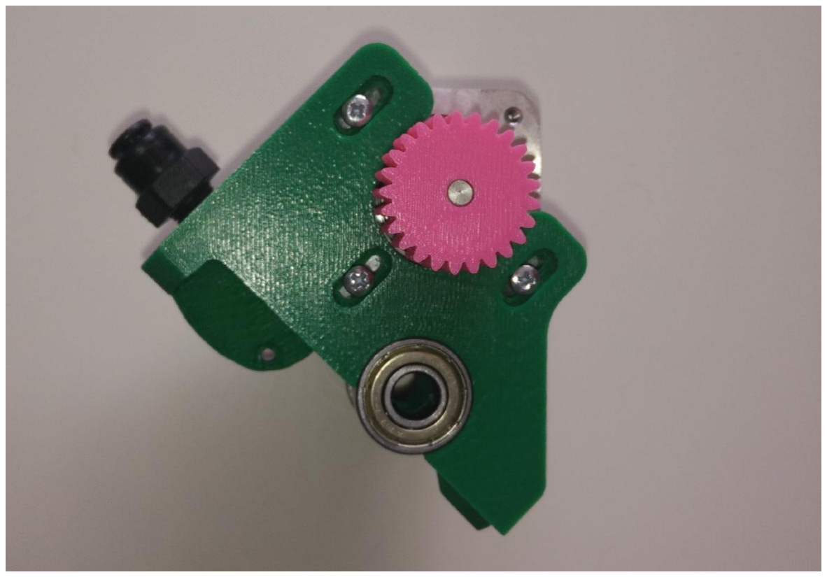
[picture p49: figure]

Gemstock 3D | Gemstruder Assembly Guide

Now remove the big gear and hobbed bolt from the body and tighten the last M3x10mm bolt into the stepper.
Don’t forget to tighten down the grub screw of the small gear. Afterwards insert the hobbed bolt back into the body.

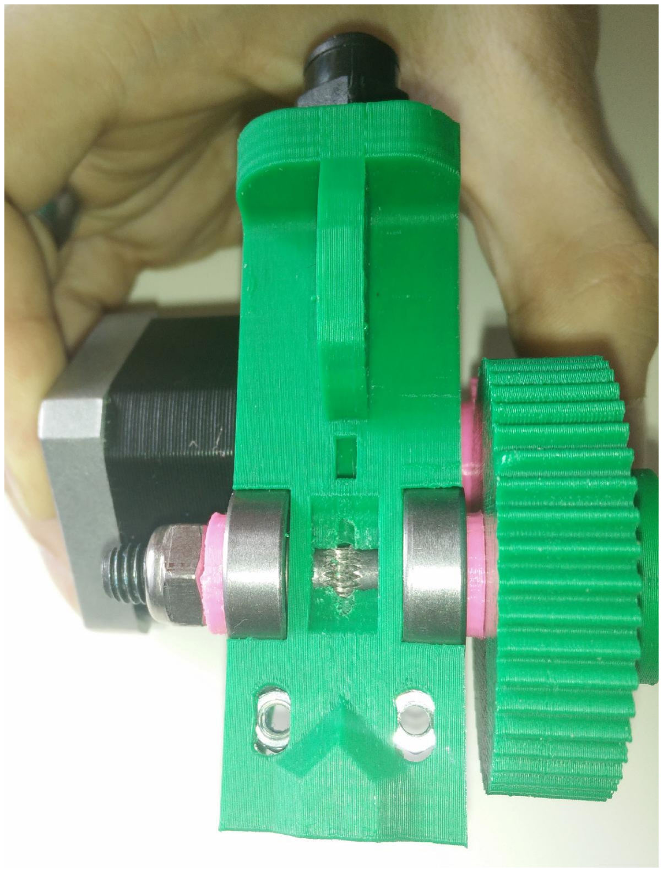
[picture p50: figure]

Gemstock 3D | Gemstruder Assembly Guide

Now we are going to fasten the hobbed bolt, grab another printed spacer (any leftover size will work) and put that on the other side of the hobbed bolt, followed by a M8 lock nut.

Heads up!
When tightening down the lock nut, make sure you eliminate play from the hobbed bolt but make sure it is still rotating freely with minimal friction.

You can lay the body aside again for a second, we will now assemble the idler.

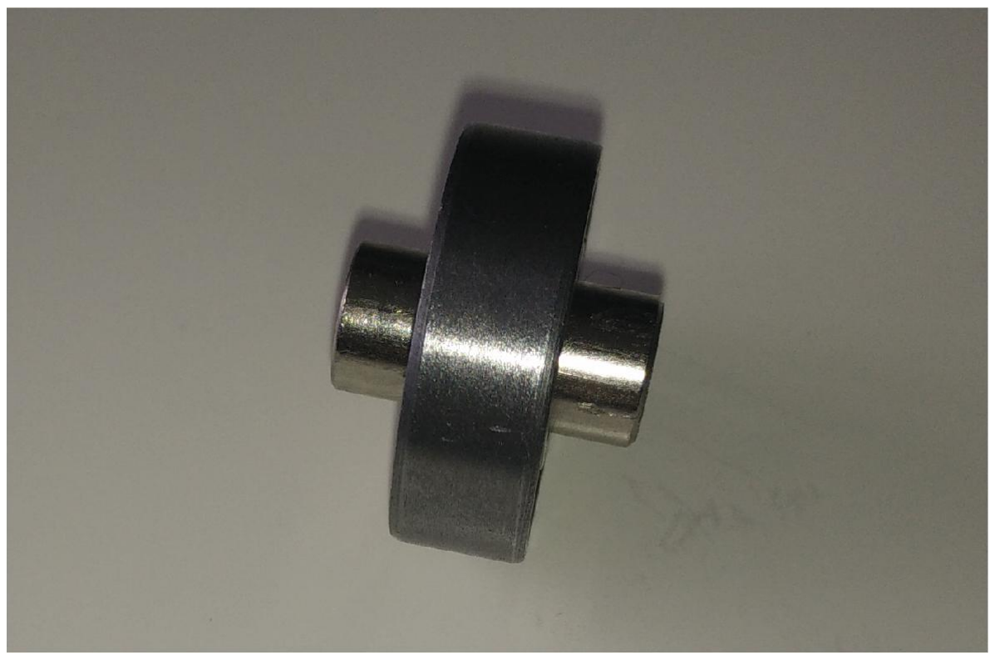
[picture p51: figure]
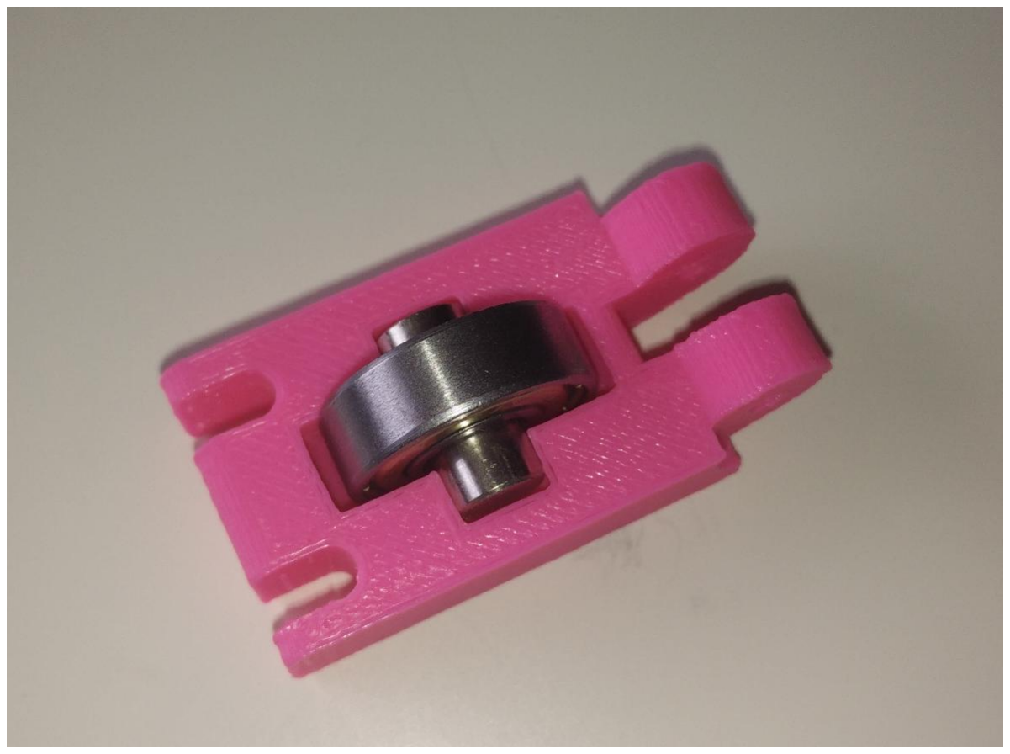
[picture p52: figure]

Gemstock 3D | Gemstruder Assembly Guide

Grab your 8x16mm smooth rod and put in into the hole of the remaining 608ZZ bearing.

Next push the bearing and smooth rod into the bottom side of the idler, it may require some force. It will snap into place.

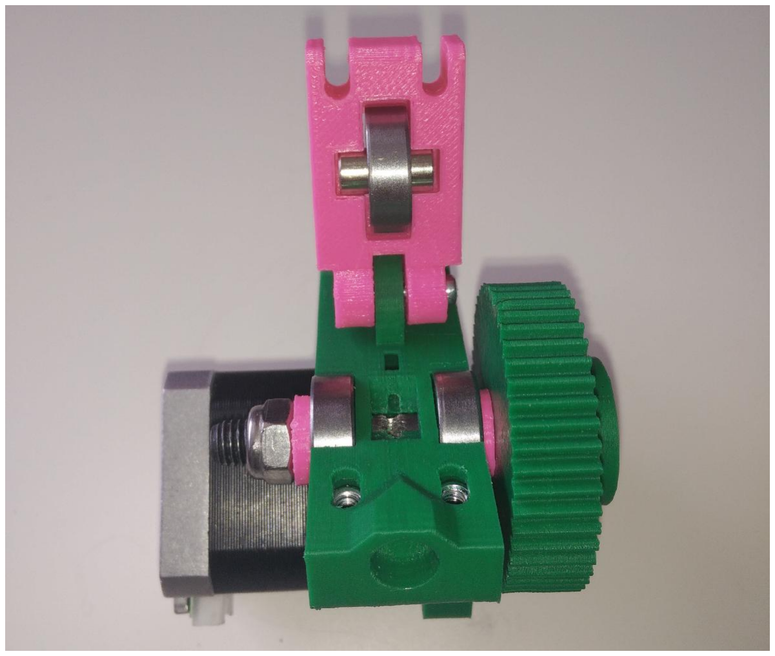
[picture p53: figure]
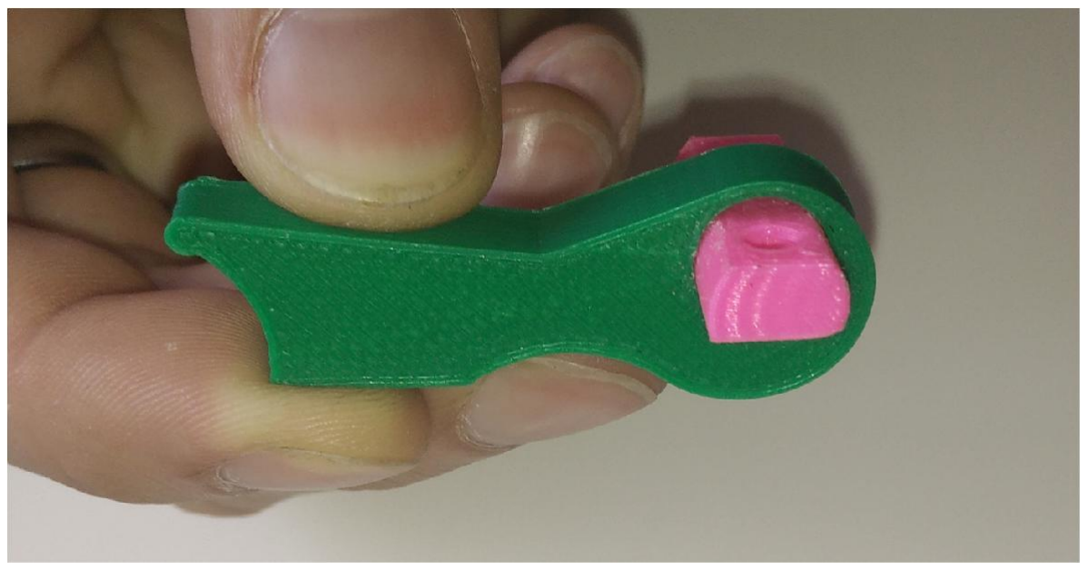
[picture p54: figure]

Gemstock 3D | Gemstruder Assembly Guide

Next grab the extruder body again and place the idler on top, use the M3x20mm bolt to mount it onto the body.

Lastly, we will mount the idler tension crossbar and lever.
Grab the lever and put the crossbar through the hole with the widest side towards the bottom of the lever.

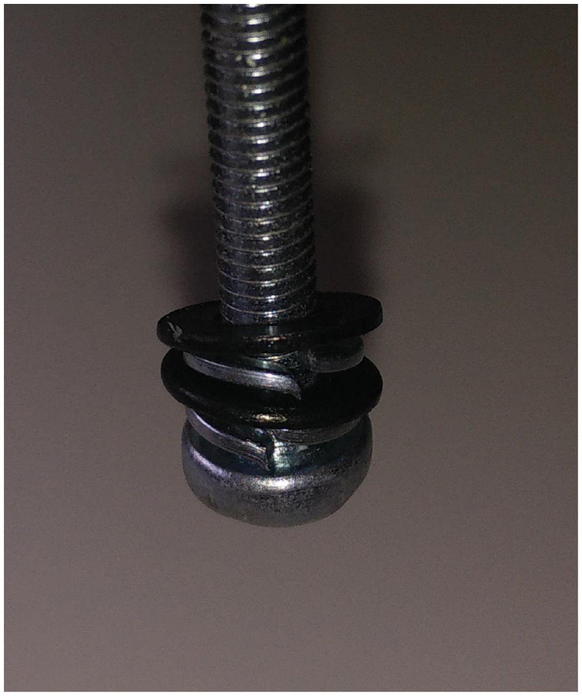
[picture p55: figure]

Gemstock 3D | Gemstruder Assembly Guide

Next, put some spring washers and regular washers onto the 2x M4x50mm bolts.
The order of washers is as followed;
1. M4x50 bolt
2. Spring washer
3. Washer
4. Spring washer
5. Washer

Then insert the M4 bolt assemblies into the holes in the crossbar with the lever in the middle and thread the M4 bolts into the lock nuts in the body. You won’t have to tighten the bolts down fully yet until you are setting your filament pressure.

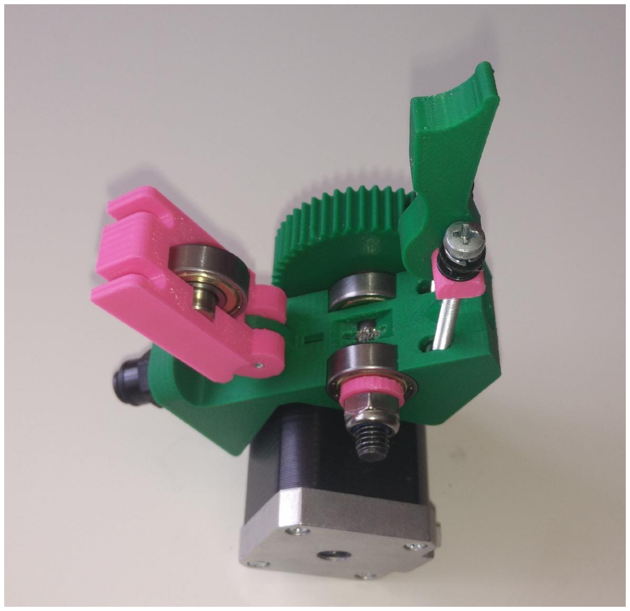
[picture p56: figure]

Gemstock 3D | Gemstruder Assembly Guide

And with that your Gemstruder is ready for mounting.

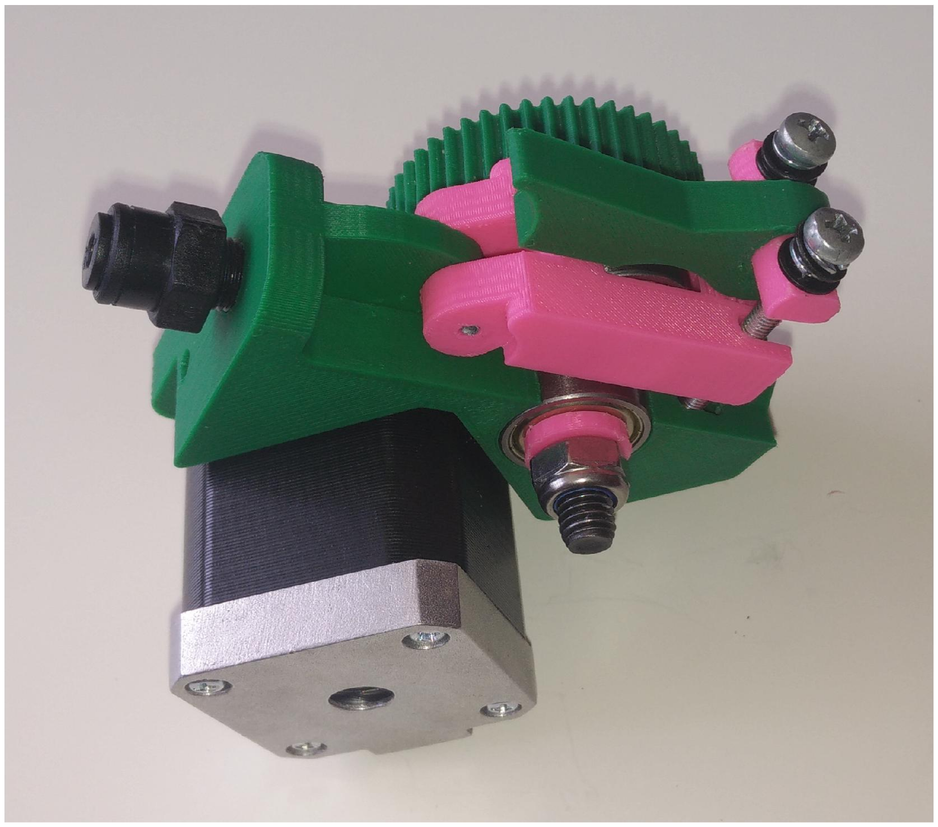
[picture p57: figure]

Gemstock 3D | Gemstruder Assembly Guide

Your main adventure can now begin.

Happy printing!

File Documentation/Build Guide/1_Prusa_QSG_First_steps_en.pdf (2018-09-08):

1

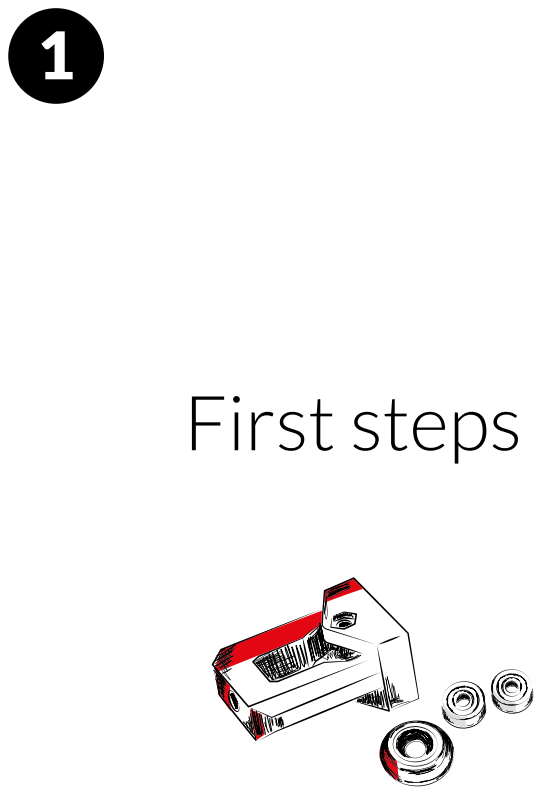
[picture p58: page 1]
First steps

# List of components – first steps

2 x Axial ball bearing B623ZZ 2 x Pulley axle X bearing B623ZZ printed part 2 x Pulley axle Y bearing B623ZZ printed part 1 x Axle X right printed part 1 x Axle X left printed part 1 x Axle X tensioner bearing B623ZZ printed part 1 x Axle X carriage A printed part 1 x Axle Y tensioner bearing B623ZZ printed part 1 x Axle Y end-stop printed part 1 x Fan support printed part 1 x LCD support printed part 1 x Hot-End safety cover printed part 17 x Nut M3 - DIN 934 class 8 black 2 x Nut M5 - DIN 934 class 8 black

*You will find the other components mentioned in these first steps in the Electronics box.

Congratulations! From now on, you are part of the RepRap community.
At bq we have opted for a free model of 3D printer with the aim of making this technology more readily available to all sections of society. We have improved it with our own designs and with those of the community in order to make its assembly and use as easy as possible, without the need for advanced technical knowledge. All you need is an idea, together with the desire to make that idea materialize. Your HEPHESTOS will take care of all the rest. We believe in a free and creative approach, whose only limitations are set by your own imagination.
We should like to thank you for choosing our Kit, and we invite you to share your experiences with us and with others, in order to participate in this very special community.
Welcome!

Visit bq.com/gb/products/prusa-hephestos.html
In this link you will find full information about Prusa i3 HEPHESTOS. Download 3D designs of the different parts and updatings of firmware, consult the 3D printing forum, play videos showing how to assemble your printer, etc.

# Kit Prusa i3 HEPHESTOS

Your Kit is comprised of the following boxes and guides:

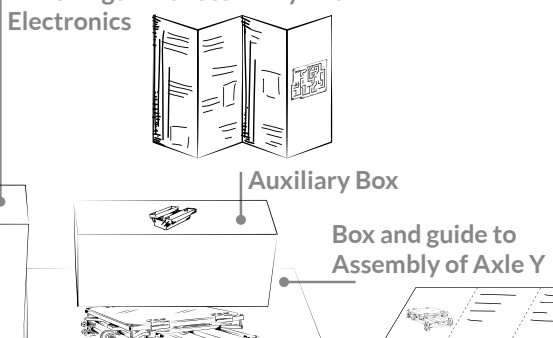
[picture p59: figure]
Auxiliary Box; Electronics; Box and guide to Assembly of Axle Y

The Kit is divided into boxes and guides which facilitate the assembly of your Prusa i3 HEPHESTOS.
We suggest you follow the steps in the numerical order that appears on the front page of each guide.
Each box contains an illustration identifying the part, which follows the order on the cover page of the assembly manual.

# Where to begin

Box and guide to assembly of the Box and guide to
assembling the
Extruder

Box and guide to
Assembly of Axle X Box and guide for Axle Z

Supplementary Box

Tool Box

First steps Box

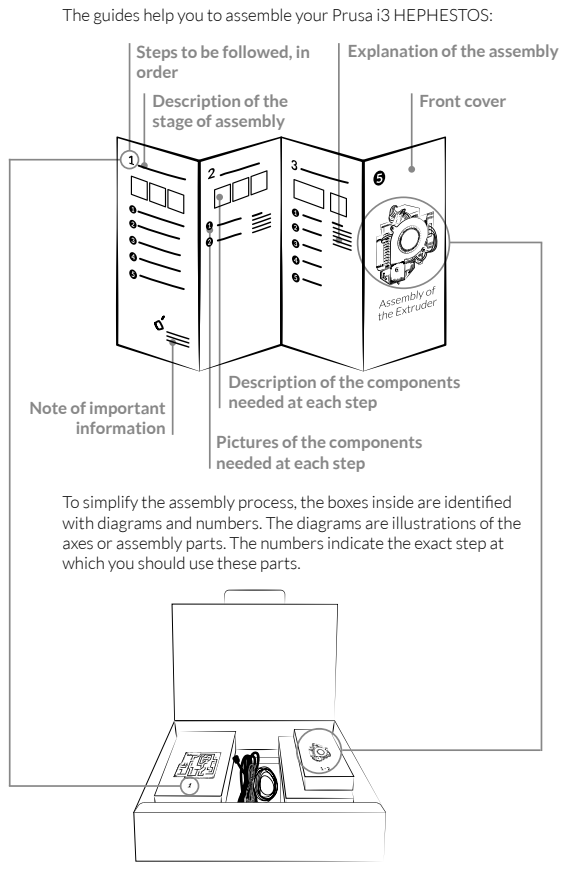
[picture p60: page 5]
Note of important; needed at each step; information; Front cover

The guides help you to assemble your Prusa i3 HEPHESTOS:

Steps to be followed, in
order
Description of the
stage of assembly

Explanation of the assembly

Description of the components

Pictures of the components
needed at each step

To simplify the assembly process, the boxes inside are identified
with diagrams and numbers. The diagrams are illustrations of the
axes or assembly parts. The numbers indicate the exact step at
which you should use these parts.

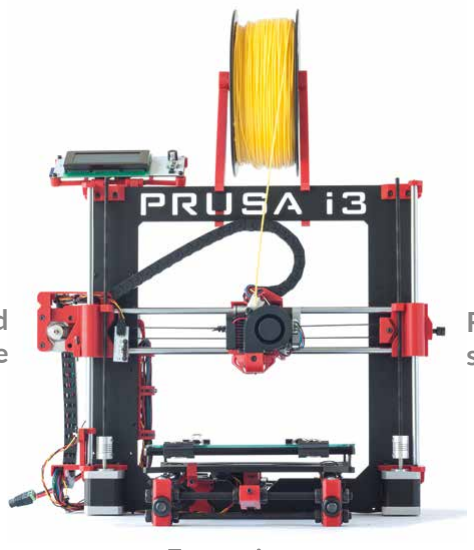
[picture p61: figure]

# Necessary tools which are not included in the Kit

# System of reference

Front view

Right-hand
side

During the assembly of your Prusa i3 HEPHESTOS we refer to the positions of the parts. Follow this diagram to position them correctly.

Left-hand
side

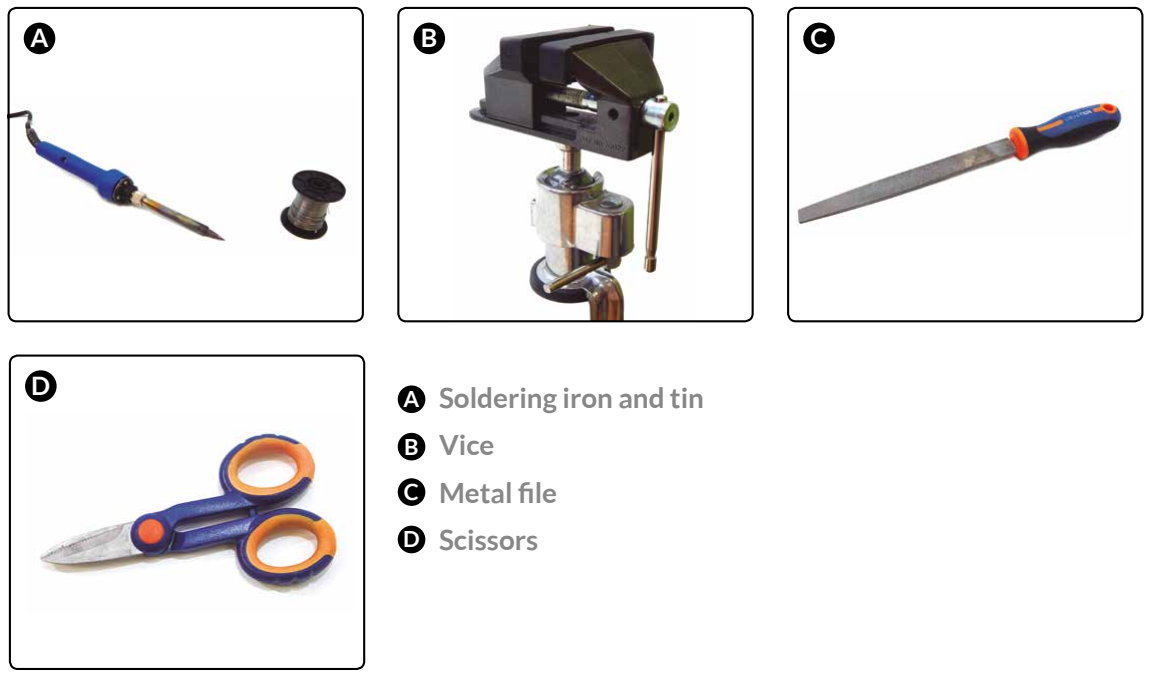
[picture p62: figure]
Soldering iron and tin; Vice; Metal file; Scissors

# Steps prior to assembly

# Preparation of the pulleys

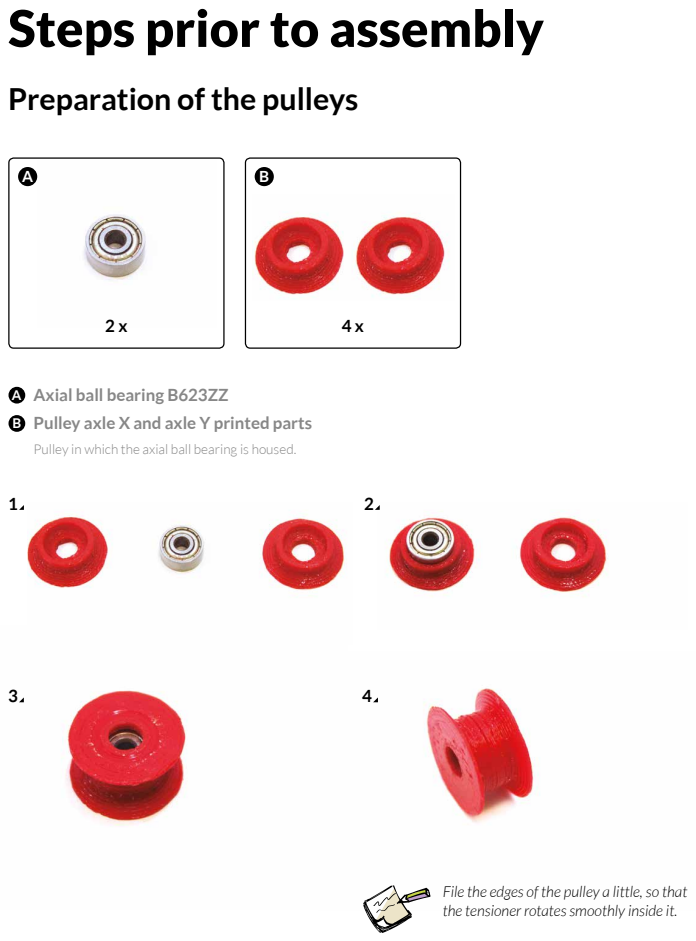
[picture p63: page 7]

Axial ball bearing B623ZZ
Pulley axle X and axle Y printed parts
Pulley in which the axial ball bearing is housed.

File the edges of the pulley a little, so that
the tensioner rotates smoothly inside it.

# Fit the nuts

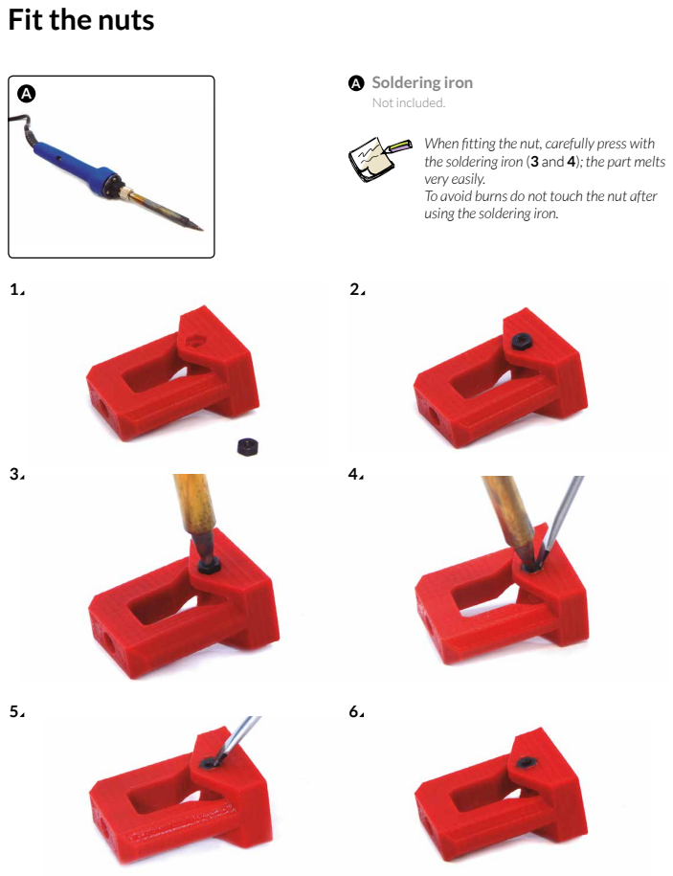
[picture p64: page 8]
Soldering iron; Not included.

When fitting the nut, carefully press with
the soldering iron (3 and 4); the part melts
very easily.
To avoid burns do not touch the nut after
using the soldering iron.

Right-hand
axle X
printed part

Part at the right-hand end of Axle X, where the belt tensioner is held.

### 1 x Nut

M5

Left-hand
axle X
printed part

Part at the left-hand end of Axle X, where the Nema 17 motor is held.

### 1 x Nut

M5

Left-hand
axle X
printed part

Part at the left-hand end of Axle X, where the Nema 17 motor is held.

### 1 x Nut

M3

Axle X
tensioner
bearing
B623ZZ
printed part

Tensioner of the Axle X belt where the axial ball bearing B623ZZ is housed together with the pulley.

### 1 x Nut

M3

Axle X
carriage A
printed part

Carriage of Axle X where the extruder is held, adapted for the use of chains.

### 2 x Nut

M3

Axle Y
tensioner
bearing
B623ZZ
printed part

Tensioner of the Axle X belt where the axial ball bearing B623ZZ is housed together
with the pulley.

### 1 x Nut

M3

Axle Y end of
basic stroke
printed part

Part located at the base of Axle Y and incorporating a screw with an M3 nut to adjust the total stroke of the axle. It is complemented by the part which holds the end-stop to the frame.

### 1 x Nut

M3

Fan support
printed part

50 x 50 mm Fan support,
located above the electronics to cool them correctly.

### 2 x Nut

M3

Fan support
printed part

50 x 50 mm Fan support,
located above the electronics to cool them correctly.

### 2 x Nut

M3

LCD panel
support
printed
part

Support for the LCD
panel. The hole for the
nuts is longer than usual
to help the nut to slide
in and position itself
correctly when the LCD
panel is screwed in.

### 4 x Nut

M3

LCD panel
support
printed
part

Support for the LCD
panel. The hole for the
nuts is longer than usual
to help the nut to slide
in and position itself
correctly when the LCD
panel is screwed in.

### 2 x Nut

M3

Hot-End
Safety
cover
printed
part

This part covers the Hot-End to prevent the user
from touching it when it’s hot, thus avoiding burns.

### 1 x Nut

M3

# Preparation of the motors

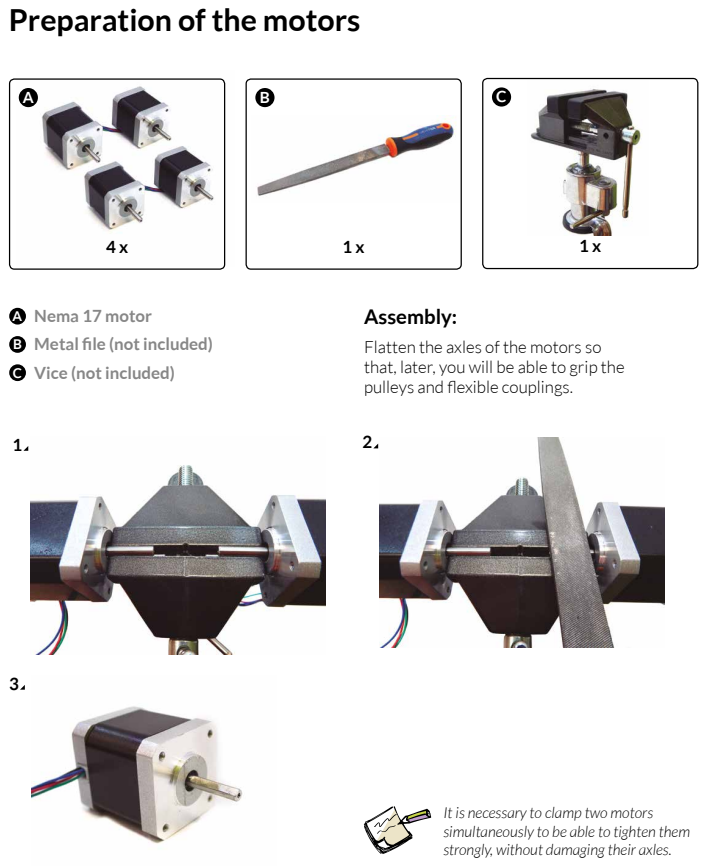
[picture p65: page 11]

Nema 17 motor
Metal file (not included)
Vice (not included)

Assembly:
Flatten the axles of the motors so
that, later, you will be able to grip the
pulleys and flexible couplings.

It is necessary to clamp two motors
simultaneously to be able to tighten them
strongly, without damaging their axles.

# Preparation of the motors’ cables

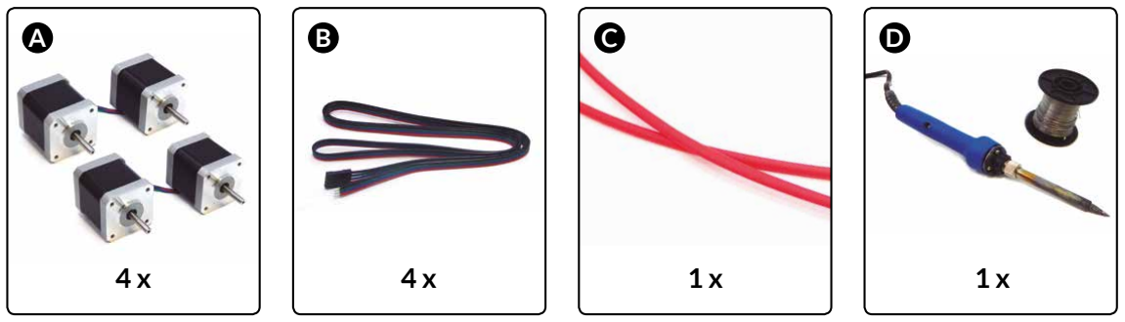
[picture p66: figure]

Nema 17 motor

Nema 17 motor (2.5A 1.8 deg/step) with female connector.
Cable for Nema 17 motor

Four-strand cable for Nema 17 bipolar step motor (2.5A 1.8 deg/step) with female connector.
Shrinkable tube

Tube of Ø 2.5 x 500 mm.
Soldering iron and tin (not included)

A

B

B

C

D

Motor Total length of motor (cm)

Length of
motor

Length of
extension
X | 85 | 30 | 55
Y | 50 | 20 | 30
Z left | 45 | 15 | 30
Z right | 65 | 30 | 35

Total length of the cables (from the base of the motor to the end of the connector)

### Assembly:

Cut four 2-cm lengths of shrinkable tubing for each of the motor’s cables (4).
Prepare the motors of Axles X and Y before beginning to assemble the printer, and the motors of Axle Z after assembling it.
(cm) | (cm)

A

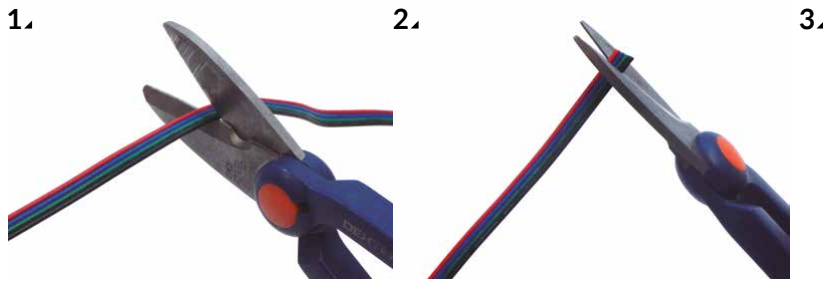
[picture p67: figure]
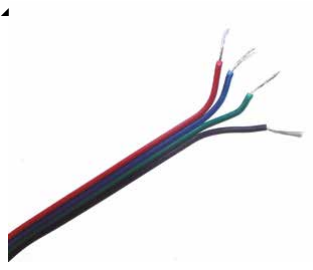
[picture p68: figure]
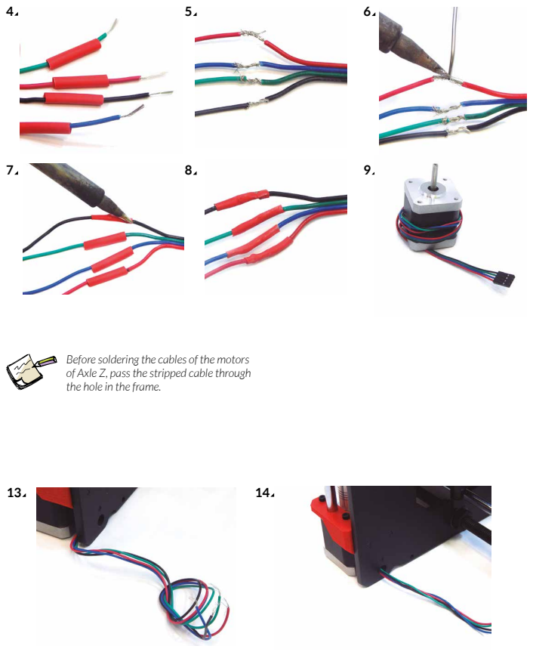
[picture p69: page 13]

Before soldering the cables of the motors
of Axle Z, pass the stripped cable through
the hole in the frame.

# Preparation of the power supply cable

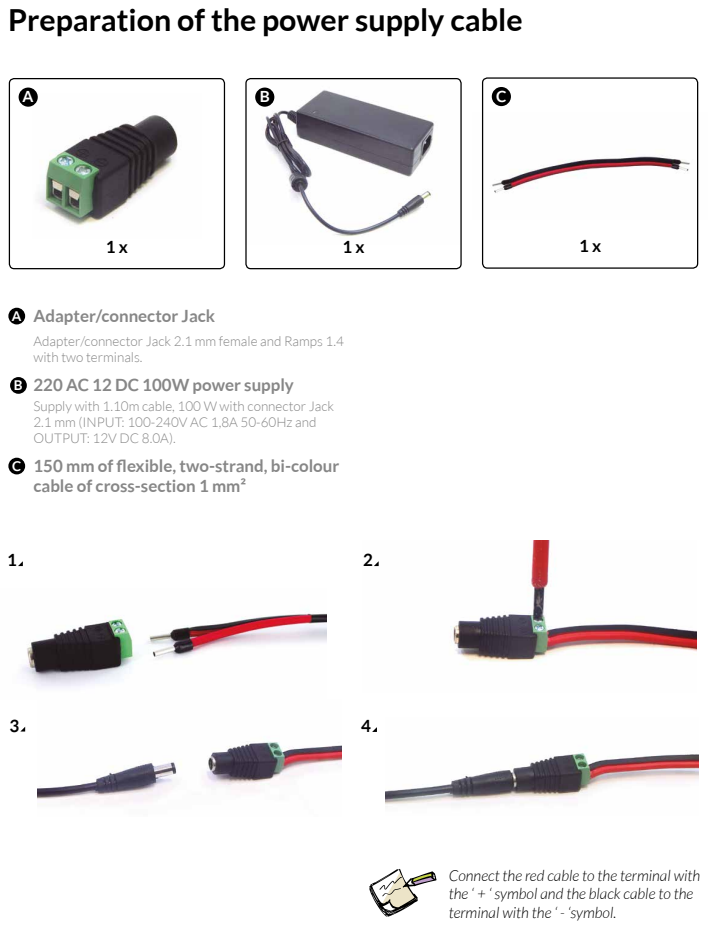
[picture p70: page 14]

Adapter/connector Jack
Adapter/connector Jack 2.1 mm female and Ramps 1.4
with two terminals.
220 AC 12 DC 100W power supply
Supply with 1.10m cable, 100 W with connector Jack
2.1 mm (INPUT: 100-240V AC 1,8A 50-60Hz and
OUTPUT: 12V DC 8.0A).
150 mm of flexible, two-strand, bi-colour
cable of cross-section 1 mm²

Connect the red cable to the terminal with
the ‘ + ‘ symbol and the black cable to the
terminal with the ‘ - ‘symbol.

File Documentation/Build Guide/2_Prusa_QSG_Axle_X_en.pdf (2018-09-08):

2

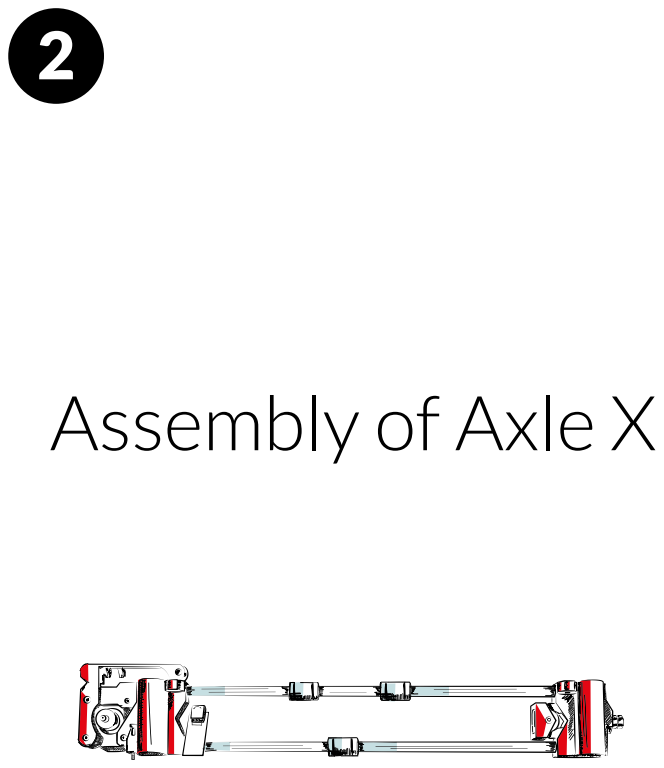
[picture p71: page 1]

Assembly of Axle X

### 2 x Smooth chrome rod Ø 8 mm x 370 mm 4 x Screw M3 x 10 mm - DIN-912 class 8.8 black 2 x Screw M3 x 16 mm - DIN-912 class 8.8 black 2 x Screw M3 x 20 mm - DIN-912 class 8.8 black 1 x Screw M3 x 25 mm - DIN-912 class 8.8 black 1 x Screw M6 x 40 mm – DIN 912 class 8.8

(with thread halfway along)

### 2 x Nut M3 - DIN 934 class 8 black 3 x Nut M6 - DIN 934 class 8 black 1 x Axle X carriage B printed part 1 x Left chain coupling axle X printed part 1 x End-Stop axle X printed part 1 x Pulley GT2 (20 teeth) 1 x Belt GT2 6 mm x 1 m 7 x Linear ball bearing LM8UU 5 x Black strap, 100 x 2.5 mm

# List of components for Axle X

1

# Inserting the bearings

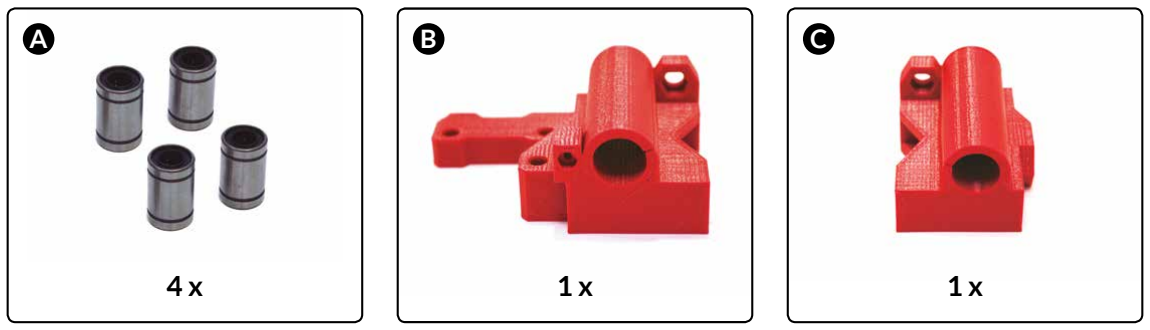
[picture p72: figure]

Linear ball bearing LM8UU
Left-hand axle X printed part
Left-hand end of Axle X, where the Nema 17 motor of that axle will be supported.
Right-hand axle X printed part
Part at the right-hand end of Axle X, where the axle’s belt tensioner will be supported.

A

B

C

In order to insert the bearings, you will first need to file down the imperfections inside the hole in the printed part, which always form in the top layers.If the bearing still does not go in, cut the closed end of the part’s base , and carefully insert the bearing.
Once the bearings have been inserted, it is advisable to insert a smooth rod, 8mm long, to ensure that the two bearings are correctly aligned.

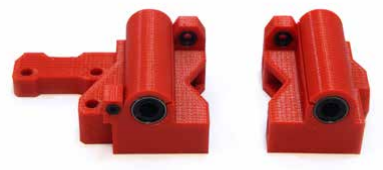
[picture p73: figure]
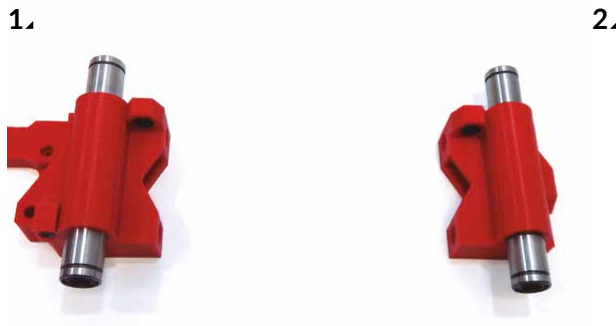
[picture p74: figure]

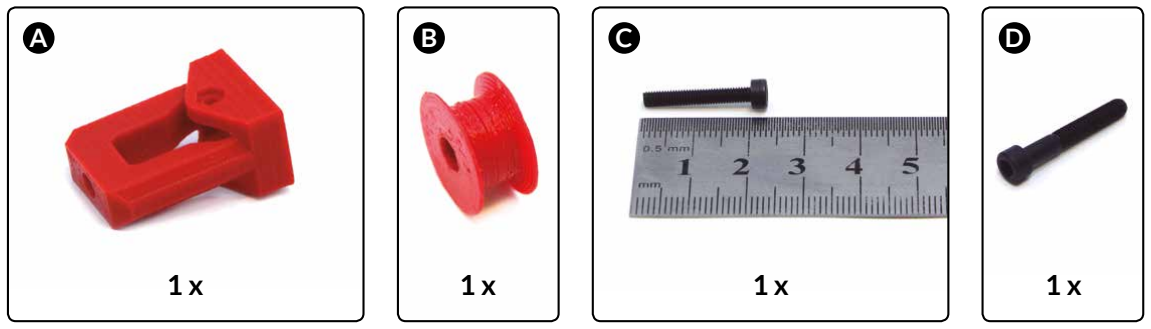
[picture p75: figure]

Bearing tensioner B623ZZ
Pulley
Screw M3 x 20 mm
Screw M6 x 40 mm (with thread halfway along its length)

A

B

C

D

2

# Preparing the Axle X tensioner

### Assembly:

Insert the screw (D) in the hole in the tensioner until it is positioned as shown in figure 2. Fix the pulley with the screw (C), as shown in figure 4.

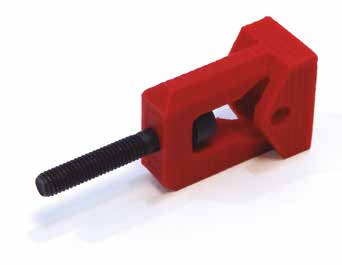
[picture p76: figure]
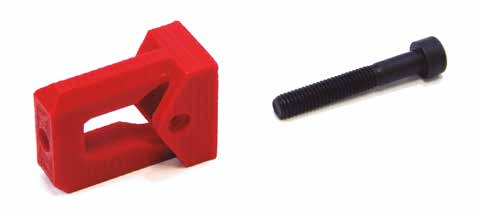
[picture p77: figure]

1 2

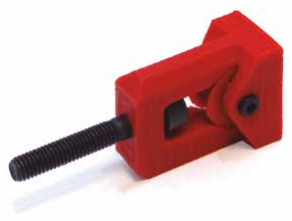
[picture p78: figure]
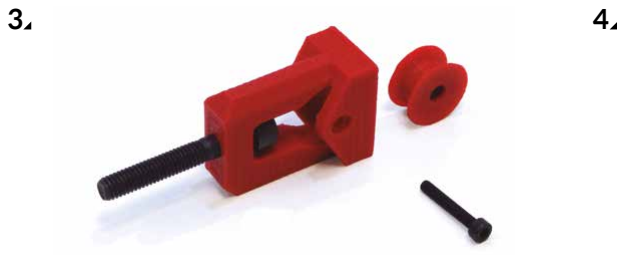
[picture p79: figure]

3

# Inserting the Axle X tensioner

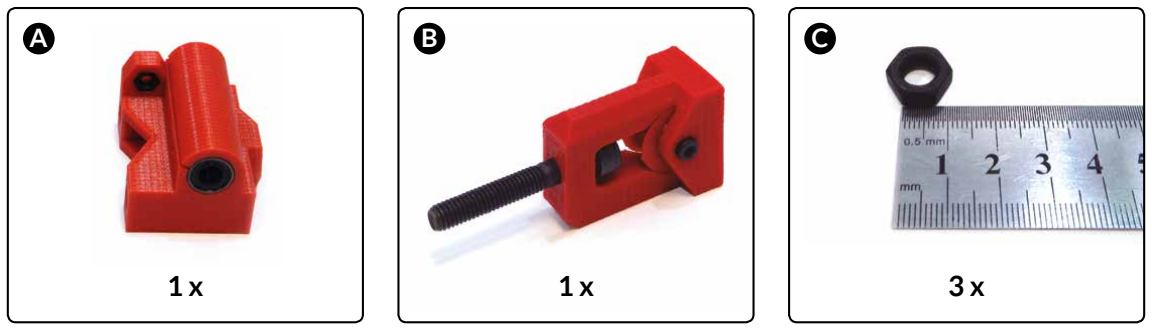
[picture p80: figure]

### Assembly:

The purpose of the tensioners is to stretch or loosen the belt once it has been fitted, in a convenient manner. File parts 1 and 2. The tensioner should slide perfectly inside the part which houses it (3). Insert the set for step 1 into the set for step 2, and screw the nuts onto the end of the screw, tightening one against the other so that the nuts remain solidly fixed to the screw. Use
a fixed spanner as a handle to slide the tensioner in a straight line.

Set for step 1
Set for step 2
Nut M6

A

B

C

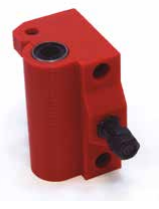
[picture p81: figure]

5


2


4

4

# Sliding the bearings onto the smooth rods


Smooth chrome rod Ø 8 x 370 mm Linear ball bearing LM8UU

A

B

2 x | 3 x

A B

1

2

5

# Preparing the End-Stop sensor


End-Stop printed part
End-stop printed part to be fastened to the smooth rod in Axle X.
End-Stop
End-Stop mounted on a PCB with an LED indicator.
Nut M3
Screw M3 x 10 mm

A

B

C

D


6

# Placing the End-Stop sensor on the smooth rod


Set for step 4
Set for step 5

A

B

### Assembly:

Place the part which you assembled in step 5 on one of the rods of step 4, specifically on that on which there is only one bearing.

1


2

# Inserting the smooth rods into the lateral parts

7


Set for step 1
Set for step 2
Set for step 3

Assembly:
Insert the ends of the rods which you prepared
in the previous step into the holes in the parts
which you prepared in step 1.

The length of the rod, once the lateral
parts have been joined onto it, should be
about 31 cm.

8

# Assembling the motor


Motor Nema 17
M3 x 16 mm Screw
M3 x 10 mm Screw
Left chain coupling axle X printed part
Coupling for holding the cable retractors in the part at
the left-hand end of Axle X.
Set for step 7

Orientate the motor’s cable by the upper
part

Assembly:
Fix the chain coupling and the motor to the set
from step 7 (E), using the screws (B and C).

9

# Inserting the adjusting screw for the End-Stop


Set for step 8
Screw M3 x 25 mm

A

B

### 1 x

B

### Assembly:

Insert the adjusting screw for the End-Stop sensor into the hole, as shown in figure 2.

# sensor

1 2

### 1 x

A

10

# Inserting the pulley into the motor


Motor Nema 17
Nema 17 bipolar step motor (2.5A 1.8 deg/
step).
Pulley GT2 (20 teeth)

Assembly:
Fix the pulley to the motor with the help of a 2
mm Allen key. Tighten the set screw against the
chamfered part of the motor’s axle.

For this step you need a 2 mm Allen key.

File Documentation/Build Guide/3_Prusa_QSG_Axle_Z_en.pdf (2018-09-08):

3


Assembly of Axle Z

2 x Smooth chrome rod Ø 8 mm x 320 mm 2 x Threaded rod M5 x 300 mm 16 x Screw M3 x 10 mm - DIN-912 class 8.8 black 2 x Screw M3 x 18 mm - DIN-912 class 8.8 black 2 x Flexible aluminium coupling 5 to 5 mm 2 x Nut M3 - DIN 934 class 8 black 1 x Upper support printed parts axle Z 1 x Lower right-hand support printed part axle Z 1 x Lower left-hand support left printed part axle Z 1 x End-stop printed part axle Z 1 x Aluminium frame

# List of components for Axle Z

1

# Attaching the motor fastener to the frame


### 6 x

Lower right-hand support printed part axle Z
Printed part to fasten the Nema 17 motor to the right-hand part of the frame, with housing for the smooth chrome rod Ø 8 mm x 320 mm.
Lower left-hand support printed part axle Z
Printed part to fasten the Nema 17 motor to the left-hand part of the frame, with housing for the smooth chrome rod Ø 8 mm x 320 mm and fastener of chain cable retractor.
Aluminium frame
Aluminium frame, powder-coated in black, with“Prusa i3” die-cut into its upper part. It has a recess in its lower part, in the area of the Y axle, to avoid rubbing once the levelling of the base has been finished.
Screw M3 x 10 mm

D

A

B

C

D


1 2


2

# Attaching the motors


Motor Nema 17
Nema 17 bipolar step motor (2.5A 1.8 deg/step).
Set for step 1
Screw M3 x 10 mm

Assembly:
Screw the motors to the supports
which you assembled in the previous
step.

Orientate the motors’
cable towards the frame
and pass them through
the hole

3

# Attaching the upper fastening of the smooth rods


Set for step 2
Upper support printed parts axle Z
Printed parts for fixing, in the upper part of the
frame, the smooth chrome rods of Ø8 mm x 320 mm
corresponding to Axle Z.
Screw M3 x 10 mm
Screw M3 x 18 mm

The M3x18 mm screw is
used to attach the LCD
support to the frame.


End-stop printed part axle Z
Part to fix the end-stop for its fastening to the smooth rod in Axle Z.
End-stop
End-stop mounted on a PCB with an LED indicator.
Nut M3
Screw M3 x 10 mm

A

B

C

D

4

# Preparing the end-stop sensor


1 | 2 | 3

5

# Joining Axle X to Axle Z: inserting threaded rods


1 x | 2 x

A B

Axle X
Threaded rod M5 x 300 mm

A

B

1 2

6

# Joining Axle X to Axle Z: inserting smooth rods


Set for steps 2 and 3
Smooth chrome rod Ø 8 mm x 320 mm

Assembly:
Insert the smooth rods so that they join the
sets of steps 2 and 3.

File the holes before you insert the rods.
Don´t insert them all the way to the
bottom.

# Joint Axle X to Axle Z: joining to Axle X

7


Set for step 6
Set for step 5

A

B

### 2 x

A B

1

2 3

### 1 x

8

# Joining of Axle X to Axle Z: flexible couplings


Set for step 7
Flexible aluminium coupling of 5 to 5 mm
Flexible aluminium couplings of 5 to 5 mm with 4 set
screws for adjusting the rods with the 2 mm Allen key.

For this step you need a 2 mm Allen key

Assembly:
Insert the flexible couplings into the axles of
the motors, and adjust them with an Allen key


Position the flexible coupling so that
the lower set screws hold the motor’s axle
and the upper ones hold the threaded rod.
When the set screws have been tightened,
make sure that the threaded rod is fixed to
the motor’s axle.

9

# Joining Axle X to Axle Z: end-stop sensor of Axle Z


Set for step 4
Set for step 8

It is advisable to stick the sets for steps 4
and 8 together with adhesive.
Remember that you have to screw the set
screw against the flat part of the motor’s
axle.

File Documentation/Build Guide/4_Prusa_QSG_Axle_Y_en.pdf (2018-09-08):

4


Assembly of Axle Y

# List of components for Axle Y

2 x Smooth chrome rod Ø 8 mm x 340 mm 2 x Threaded rod M10 x 370 mm 4 x Black threaded rod M8 x 205 mm 1 x Screw M3 x 16 mm - DIN-912 class 8.8 black 6 x Screw M3 x 25 mm - DIN-912 class 8.8 black 7 x Screw M3 x 10 mm - DIN-912 class 8.8 black 1 x Screw M3 x 20 mm - DIN-912 class 8.8 black 5 x Nut M3 - DIN 934 class 8 black 22 x Nut M8 - DIN 934 class 8 black 8 x Nut M10 - DIN 934 class 8 black 4 x Nut M10 DIN 6923 class 8 black, serrated 22 x Washer M8 - DIN-125 class 6 black 8 x Washer M10 - DIN-125 class 6 black 4 x Washer M10 (Ø exterior 30 mm) DIN-9021 black 1 x Belt-holding printed part axle Y 1 x Motor printed part axle Y 4 x Corner printed part axle Y 1 x End-stop frame printed part axle Y 1 x Axial ball bearing B623ZZ 1 x Pulley GT2 (20 teeth) 1 x Belt GT2 6 mm x 1 m 1 x Aluminium base 1 x Aluminium frame 1 x Methacrylate base 3 x Linear ball bearing LM8UU 1 x Glass piece 220 x 220 x 3 mm 4 x Spring (length: 30.5 mm, external Ø : 4.5 mm and thickness:

0.45 mm)

### 4 x Black binder clip (35 x 10 mm) 11 x Black strap 100 x 2.5 mm

1

# Preparing the threaded rods

4 x | 4 x

### 2 x

4 x | 4 x

Nut M10
Washer M10
Washer M10 (Ø exterior 30 mm) Nut M10 (serrated)
Threaded rod M10 x 370 mm

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
# Preparing the smooth rods


2 x | 3 x

Smooth chrome rod Ø 8 x 340 mm Linear ball bearing LM8UU

A B

A

B

1

2

3

# Joining the rods

4 x | 1 x | 1 x

Corner printed part axle Y
Corners which form the base and the structure of Axle Y
Set for step 1
Set for step 2
A | B | C

A

B

C

1

2

### Assembly:

Join the ends of sets B and C to the parts which form the corners.

4

# Fixing with nuts


4 x | 4 x

Nut M10
Washer M10

A B

A

B

1

2

### Assembly:

Tighten the washers and nuts at the ends of the rods so that the part is well fastened.

5

# Fixing with straps

### 4 x

Black strap 100 x 2.5 mm

A

A

1

3

2

### Assembly:

Fix the smooth rods by positioning the flanges as shown in the figures.

6

# Preparing the tensioner

Pulley; Bearing tensioner B623ZZ printed part axle Y; Screw M3 x 20 mm; Screw M3 x 25 mm; Nut M3

### Assembly:

Screw the long screw (D) through the pulley and fix it with the two nuts. Insert the short screw (C) into the bearing tensioner as shown in the picture.


7

# Preparing the motor


Motor Nema 17
Nema 17 bipolar step motor
(2.5A 1.8 deg/step)
Motor printed part axle Y
Printed part to fasten the Nema 17 motor of Axle Y to
the threaded rods
Screw M3 x 10 mm

Make sure that the orientation of the
motor is correct.

8

# Preparing the threaded rods (Part 1)

Washer M8; Nut M8; Set for step 6; Set for step 7

Threaded rod M8 x 205 mm

### Assembly:

Fix the step 7 set to two of the threaded rods, securing them with the washers and nuts. Do the same with the step 6 set.


12

9

# Preparing the threaded rods (Part 2)

1 x | 8 x

Set for step 8
Washer M8
Nut M8

A B

A

B

C

### 8 x

C

1

### Assembly:

Put the washers and nuts onto the set which you assembled in the previous step, as shown in the picture.


2

10

# Joining the rods


1 x | 1 x

Set for step 9
Set for step 5

A B

A

B

1

2

### Assembly:

Fit together the four sets which you assembled in previous steps, by inserting the ends of the rods into the holes in the printed parts of the corners.

11

# Fixing the structure

8 x | 8 x | 1 x
A | B | C

Nut M8
Washer M8
Set for step 10

A

B

C

1

2

12

# Preparing the aluminium base


1 x | 1 x | 2 x
A | B | C

Aluminium base
Belt-holding pirnted part axle Y
Part for holding the belt GT2 corresponding to Axle Y
Screw M3 x 10 mm

A

B

C

1

2

### Assembly:

Screw the printed part which will hold the belt onto the aluminium base.

13

# Fixing the aluminium base with straps

1 x | 1 x | 3 x

Set for step 11
Set for step 12
Black strap 100 x 2,5 mm
A | B | C

A

B

C

1

2

### Assembly:

Join the sets for steps 11 and 12, fastening the ends with the straps.


35

46

7

14

# Preparing the end-stop sensor of the base


1 x | 1 x

End-stop printed part axle Y (base)
The part which is located on the base of Axle Y and which incorporates a screw with M3 nut to adjust the total stroke of the axle. It is completed by the part which holds the end-stop part to the frame.
Screw M3 x 25 mm

A B

A

B

1 2

15

# Anchoring the end-stop sensor to the base

1 x | 1 x

Set for step 13
Set for step 14

A B

A

B

1 2

3 4

16

# Fitting the Axle Y belt


### Assembly:

Turn the set over and put the pulley onto the motor’s axle, tightening it with the Allen key (3). Loosen the screw to slacken the tensioner (5), and fit the belt (6). When the belt has been fitted, cut off the remaining part (7, 8, 9, 10, 11). Align the belt (12, 13). Tighten it by turning the screw of the tensioner with the 2 mm Allen key (14).

1 x | 1 x | 4 x

Belt GT2 6 mm x 1 m
Pulley GT2 (20 teeeth)
Black strap 100 x 2,5 mm
A | B | C

A

B

C

1 3

5

2

4

For this step you will need a 2 mm Allen key.


6

7 | 8 | 9

10 11


12 13

14

17

# Tightening all the nuts

Printed fixed spanner 10 (M6), 13 (M8), 17 (M10)

Assembly:
Tighten all the nuts with the printed fixed
spanner. Check that the base slides well with
the smooth rods.

You need to file the imperfections of the
fixed spanner to make it fit well on the
nuts.

18

# Fitting the methacrylate base

1 x | 4 x | 4 x

Methacrylate base
Springs
Screw M3 x 25 mm
A | B | C

A

B

C

### Assembly:

Fix the methacrylate base to the structure which you assembled in previous steps. To do this, join the four corners of the methacrylate base to the four sides of the aluminium base, using the screws and the springs.

1 2

19

# Preparing the end-stop sensor in the frame


2 x | 2 x | 1 x | 1 x

Nut M3
Screw M3 x 10 mm
End-stop frame printed part axle Y
The part which fastens the Y axle’s end-stop to the frame. It is completed by the base part which is adjustable with the screw and M3 nut.
End-stop frame
The end-stop part mounted on a PCB with an LED indicator.
A | B | C | D

A

B

C

D

1

2

20

# Anchoring the end-stop sensor to the frame

1 x | 1 x | 1 x | 1 x

Set for step 19
Nut M3
Screw M3 x 16 mm
Black aluminium frame
A | B | C | D

A

B

C

D

1 2


3 4

5

21

# Joining of Axle Y with Axles X and Z (Part 1)

Axle Y; Axle X and Z

The distance from the aluminium frame to
the printed part has to be 9.1 cm.

22

# Joining of Axle Y with Axles Ejes X and Z (Part 2)


Set for step 21
Printed fixed spanner 10 (M6), 13 (M8), 17 (M10)

A

B

1 x | 1 x

A B

1

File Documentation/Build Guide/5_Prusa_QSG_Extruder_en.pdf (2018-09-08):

5


Assembly of the
Extruder

### 1 x Witbox extruder 1 x Extruder bracket 2 x Screw M4 x 6 mm DIN-912 class 8.8

(with head for Allen 2.5 mm)

### 2 x Screw M3 x 10 mm - DIN-912 class 8.8 black 1 x Screw M3 x 20 mm - DIN-912 class 8.8 black 1 x Nut M3 - DIN 934 class 8 black

# List of components for the Extruder

1

# Preparing the carriage

Axle X carriage A printed part; for the use of chains. Axle X carriage B printed part; Screw M3 x 20 mm; Nut M3

Carriage of axle X where the extruder is held, adapted

Part for fastening the belt of Axle X to the carriage.


2

# Mounting the carriage on Axle X


### Assembly:

Fit the set for step 1 onto the smooth rods of Axle X.

1 x | 1 x

Prusa with all the axles
Set for step 1

A B

A

B

1 2

3 4

3

# Securing the carriage with a strap


Set for step 2
Black strap 100 x 2.5 mm

A

B

1 x | 1 x

A B

1 | 2 | 3

4 5

4

# Fitting the Axle X belt

Belt GT2 6 mm x 1 m; Set for step 3; Black strap 100 x 2.5 mm; Printed fixed spanner

Assembly:
Pass the belt round the pulley of the right-hand
printed part, then round the set for step 3, and
finally round the pulley of the left-hand printed
part of Axle X. Tighten the belt and fix it with
the straps.

Use the printed fixed spanner as a
handle with the tensioner to tighten the
belt

5

# Mounting the extruder bracket


### 1 x

A


### 2 x

B

Extruder bracket
A metal bracket which allows the extruder to be fastened to the carriage of Axle X by means of two screws in the frame.
Screw M3 x 10 mm

A

B

### Assembly:

Screw the extruder bracket to the part which you assembled in the first step.


# Mounting the extruder

6


Witbox Extruder
Witbox Extruder (direct extrusion by filament of 1.75 mm with 0.4 mm nozzle).
Screw M4 x 6 mm

A

B

1 x | 2 x

A B

1

2

### Assembly:

First, remove the nozzle. Using the screws, fix the extruder to the bracket which you mounted in the previous step.

7

# Fitting the nozzle and the protector


Hot-End Protector printed part
This part covers the Hot-End to prevent the user from touching it when it’s hot, thus avoiding burns.
Nozzle printed part
Screw M3 x 20 mm

A

B

C

### Assembly:

Connect the nozzle to the protector and fasten it round the Hot-End with a screw.


This screw (C) is not the same one that was
screwed to the nozzle in the previous step.


1 | 2 | 3

The Hot-End’s safety protector is an optional extra which is not essential for the functioning of the printer, but its use is strongly recommended for the avoidance of burns.

8

# Fit the glass of the base


Glass 220 x 220 x 3 mm
Black Binder (35 x 10 mm)

A

B

1 x | 4 x

A B

### Assembly:

Place the glass on the aluminium base, fixing it with the four clips.

1 2

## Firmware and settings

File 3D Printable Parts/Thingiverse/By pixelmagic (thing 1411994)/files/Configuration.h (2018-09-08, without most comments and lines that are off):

#define CONFIGURATION_H
#define NUM_EXTRUDER 1
#define MOTHERBOARD 33
#include "pins.h"
#define FAN_BOARD_PIN -1
#define X_MAX_PIN ORIG_X_MIN_PIN
#define Y_MAX_PIN ORIG_Y_MIN_PIN
#define Z_MAX_PIN ORIG_Z_MIN_PIN
#define BLUETOOTH_SERIAL  -1
#define BLUETOOTH_BAUD  115200
#define MIXING_EXTRUDER 0
#define DRIVE_SYSTEM 0
#define XAXIS_STEPS_PER_MM 79.6138
#define YAXIS_STEPS_PER_MM 79.6138
#define ZAXIS_STEPS_PER_MM 4000
#define EXTRUDER_FAN_COOL_TEMP 50
#define PDM_FOR_EXTRUDER 0
#define PDM_FOR_COOLER 0
#define DECOUPLING_TEST_MAX_HOLD_VARIANCE 20
#define DECOUPLING_TEST_MIN_TEMP_RISE 1
#define KILL_IF_SENSOR_DEFECT 0
#define RETRACT_ON_PAUSE 2
#define PAUSE_START_COMMANDS ""
#define PAUSE_END_COMMANDS ""
#define EXT0_X_OFFSET 0
#define EXT0_Y_OFFSET 0
#define EXT0_Z_OFFSET 0
#define EXT0_STEPS_PER_MM 94.196
#define EXT0_TEMPSENSOR_TYPE 1
#define EXT0_TEMPSENSOR_PIN TEMP_0_PIN
#define EXT0_HEATER_PIN HEATER_0_PIN
#define EXT0_STEP_PIN ORIG_E0_STEP_PIN
#define EXT0_DIR_PIN ORIG_E0_DIR_PIN
#define EXT0_INVERSE 0
#define EXT0_ENABLE_PIN ORIG_E0_ENABLE_PIN
#define EXT0_ENABLE_ON 0
#define EXT0_MAX_FEEDRATE 25
#define EXT0_MAX_START_FEEDRATE 20
#define EXT0_MAX_ACCELERATION 5000
#define EXT0_HEAT_MANAGER 3
#define EXT0_WATCHPERIOD 1
#define EXT0_PID_INTEGRAL_DRIVE_MAX 230
#define EXT0_PID_INTEGRAL_DRIVE_MIN 40
#define EXT0_PID_PGAIN_OR_DEAD_TIME 7
#define EXT0_PID_I 2
#define EXT0_PID_D 40
#define EXT0_PID_MAX 255
#define EXT0_ADVANCE_K 0
#define EXT0_ADVANCE_L 0
#define EXT0_ADVANCE_BACKLASH_STEPS 0
#define EXT0_WAIT_RETRACT_TEMP 150
#define EXT0_WAIT_RETRACT_UNITS 0
#define EXT0_SELECT_COMMANDS ""
#define EXT0_DESELECT_COMMANDS ""
#define EXT0_EXTRUDER_COOLER_PIN ORIG_FAN2_PIN
#define EXT0_EXTRUDER_COOLER_SPEED 255
#define EXT0_DECOUPLE_TEST_PERIOD 12000
#define EXT0_JAM_PIN -1
#define EXT0_JAM_PULLUP 0
#define FEATURE_RETRACTION 1
#define AUTORETRACT_ENABLED 0
#define RETRACTION_LENGTH 3
#define RETRACTION_LONG_LENGTH 13
#define RETRACTION_SPEED 40
#define RETRACTION_Z_LIFT 0
#define RETRACTION_UNDO_EXTRA_LENGTH 0
#define RETRACTION_UNDO_EXTRA_LONG_LENGTH 0
#define RETRACTION_UNDO_SPEED 20
#define FILAMENTCHANGE_X_POS 0
#define FILAMENTCHANGE_Y_POS 0
#define FILAMENTCHANGE_Z_ADD  2
#define FILAMENTCHANGE_REHOME 1
#define FILAMENTCHANGE_SHORTRETRACT 5
#define FILAMENTCHANGE_LONGRETRACT 50
#define JAM_STEPS 220
#define JAM_SLOWDOWN_STEPS 320
#define JAM_SLOWDOWN_TO 70
#define JAM_ERROR_STEPS 500
#define JAM_MIN_STEPS 10
#define JAM_ACTION 0
#define RETRACT_DURING_HEATUP true
#define PID_CONTROL_RANGE 20
#define SKIP_M109_IF_WITHIN 2
#define SCALE_PID_TO_MAX 0
#define TEMP_HYSTERESIS 0
#define EXTRUDE_MAXLENGTH 160
#define NUM_TEMPS_USERTHERMISTOR0 0
#define USER_THERMISTORTABLE0 {}
#define NUM_TEMPS_USERTHERMISTOR1 0
#define USER_THERMISTORTABLE1 {}
#define NUM_TEMPS_USERTHERMISTOR2 0
#define USER_THERMISTORTABLE2 {}
#define GENERIC_THERM_VREF 5
#define GENERIC_THERM_NUM_ENTRIES 33
#define HEATER_PWM_SPEED 0
#define HAVE_HEATED_BED 1
#define HEATED_BED_MAX_TEMP 120
#define SKIP_M190_IF_WITHIN 3
#define HEATED_BED_SENSOR_TYPE 1
#define HEATED_BED_SENSOR_PIN TEMP_1_PIN
#define HEATED_BED_HEATER_PIN HEATER_1_PIN
#define HEATED_BED_SET_INTERVAL 5000
#define HEATED_BED_HEAT_MANAGER 0
#define HEATED_BED_PID_INTEGRAL_DRIVE_MAX 255
#define HEATED_BED_PID_INTEGRAL_DRIVE_MIN 80
#define HEATED_BED_PID_PGAIN_OR_DEAD_TIME   196
#define HEATED_BED_PID_IGAIN   33
#define HEATED_BED_PID_DGAIN 290
#define HEATED_BED_PID_MAX 255
#define HEATED_BED_DECOUPLE_TEST_PERIOD 300000
#define MIN_EXTRUDER_TEMP 170
#define MAXTEMP 250
#define MIN_DEFECT_TEMPERATURE 5
#define MAX_DEFECT_TEMPERATURE 290
#define ENDSTOP_PULLUP_X_MIN true
#define ENDSTOP_X_MIN_INVERTING true
#define MIN_HARDWARE_ENDSTOP_X true
#define ENDSTOP_PULLUP_Y_MIN true
#define ENDSTOP_Y_MIN_INVERTING true
#define MIN_HARDWARE_ENDSTOP_Y true
#define ENDSTOP_PULLUP_Z_MIN true
#define ENDSTOP_Z_MIN_INVERTING true
#define MIN_HARDWARE_ENDSTOP_Z true
#define ENDSTOP_PULLUP_X_MAX true
#define ENDSTOP_X_MAX_INVERTING false
#define MAX_HARDWARE_ENDSTOP_X false
#define ENDSTOP_PULLUP_Y_MAX true
#define ENDSTOP_Y_MAX_INVERTING false
#define MAX_HARDWARE_ENDSTOP_Y false
#define ENDSTOP_PULLUP_Z_MAX true
#define ENDSTOP_Z_MAX_INVERTING false
#define MAX_HARDWARE_ENDSTOP_Z false
#define max_software_endstop_r true
#define min_software_endstop_x false
#define min_software_endstop_y false
#define min_software_endstop_z false
#define max_software_endstop_x true
#define max_software_endstop_y true
#define max_software_endstop_z true
#define ENDSTOP_X_BACK_MOVE 5
#define ENDSTOP_Y_BACK_MOVE 5
#define ENDSTOP_Z_BACK_MOVE 2
#define ENDSTOP_X_RETEST_REDUCTION_FACTOR 3
#define ENDSTOP_Y_RETEST_REDUCTION_FACTOR 3
#define ENDSTOP_Z_RETEST_REDUCTION_FACTOR 3
#define ENDSTOP_X_BACK_ON_HOME 1
#define ENDSTOP_Y_BACK_ON_HOME 1
#define ENDSTOP_Z_BACK_ON_HOME 0
#define ALWAYS_CHECK_ENDSTOPS 0
#define X_ENABLE_ON 0
#define Y_ENABLE_ON 0
#define Z_ENABLE_ON 0
#define DISABLE_X 0
#define DISABLE_Y 0
#define DISABLE_Z 0
#define DISABLE_E 0
#define INVERT_X_DIR 1
#define INVERT_Y_DIR 0
#define INVERT_Z_DIR 1
#define X_HOME_DIR -1
#define Y_HOME_DIR -1
#define Z_HOME_DIR -1
#define X_MAX_LENGTH 215
#define Y_MAX_LENGTH 210
#define Z_MAX_LENGTH 180
#define X_MIN_POS 0
#define Y_MIN_POS 0
#define Z_MIN_POS 0
#define DISTORTION_CORRECTION 0
#define DISTORTION_CORRECTION_POINTS 5
#define DISTORTION_CORRECTION_R 100
#define DISTORTION_PERMANENT 1
#define DISTORTION_UPDATE_FREQUENCY 15
#define DISTORTION_START_DEGRADE 0.5
#define DISTORTION_END_HEIGHT 1
#define DISTORTION_EXTRAPOLATE_CORNERS 0
#define FEATURE_BABYSTEPPING 1
#define BABYSTEP_MULTIPLICATOR 1
#define DELTA_SEGMENTS_PER_SECOND_PRINT 180 // Move accurate setting for print moves
#define DELTA_SEGMENTS_PER_SECOND_MOVE 70 // Less accurate setting for other moves
#define DELTA_HOME_ON_POWER 0
#define DELTASEGMENTS_PER_PRINTLINE 24
#define STEPPER_INACTIVE_TIME 360L
#define MAX_INACTIVE_TIME 0L
#define MAX_FEEDRATE_X 250
#define MAX_FEEDRATE_Y 250
#define MAX_FEEDRATE_Z 3.3
#define HOMING_FEEDRATE_X 50
#define HOMING_FEEDRATE_Y 50
#define HOMING_FEEDRATE_Z 4
#define HOMING_ORDER HOME_ORDER_XYZ
#define ZHOME_MIN_TEMPERATURE 0
#define ZHOME_HEAT_ALL 1
#define ZHOME_HEAT_HEIGHT 20
#define ZHOME_X_POS 999999
#define ZHOME_Y_POS 999999
#define ENABLE_BACKLASH_COMPENSATION 0
#define X_BACKLASH 0
#define Y_BACKLASH 0
#define Z_BACKLASH 0
#define RAMP_ACCELERATION 1
#define STEPPER_HIGH_DELAY 0
#define DIRECTION_DELAY 0
#define STEP_DOUBLER_FREQUENCY 12000
#define ALLOW_QUADSTEPPING 1
#define DOUBLE_STEP_DELAY 0 // time in microseconds
#define MAX_ACCELERATION_UNITS_PER_SQ_SECOND_X 1000
#define MAX_ACCELERATION_UNITS_PER_SQ_SECOND_Y 1000
#define MAX_ACCELERATION_UNITS_PER_SQ_SECOND_Z 100
#define MAX_TRAVEL_ACCELERATION_UNITS_PER_SQ_SECOND_X 1000
#define MAX_TRAVEL_ACCELERATION_UNITS_PER_SQ_SECOND_Y 1000
#define MAX_TRAVEL_ACCELERATION_UNITS_PER_SQ_SECOND_Z 100
#define MAX_JERK 10
#define MAX_ZJERK 0.4
#define PRINTLINE_CACHE_SIZE 16
#define MOVE_CACHE_LOW 10
#define LOW_TICKS_PER_MOVE 250000
#define FEATURE_TWO_XSTEPPER 0
#define X2_STEP_PIN   ORIG_E1_STEP_PIN
#define X2_DIR_PIN    ORIG_E1_DIR_PIN
#define X2_ENABLE_PIN E1_ENABLE_PIN
#define FEATURE_TWO_YSTEPPER 0
#define Y2_STEP_PIN   ORIG_E1_STEP_PIN
#define Y2_DIR_PIN    ORIG_E1_DIR_PIN
#define Y2_ENABLE_PIN E1_ENABLE_PIN
#define FEATURE_TWO_ZSTEPPER 0
#define Z2_STEP_PIN   ORIG_E1_STEP_PIN
#define Z2_DIR_PIN    ORIG_E1_DIR_PIN
#define Z2_ENABLE_PIN E1_ENABLE_PIN
#define FEATURE_DITTO_PRINTING 0
#define USE_ADVANCE 0
#define ENABLE_QUADRATIC_ADVANCE 0
#define BAUDRATE 115200
#define ENABLE_POWER_ON_STARTUP 1
#define POWER_INVERTING 0
#define KILL_METHOD 1
#define ACK_WITH_LINENUMBER 1
#define WAITING_IDENTIFIER "wait"
#define ECHO_ON_EXECUTE 1
#define EEPROM_MODE 2
#define PS_ON_PIN ORIG_PS_ON_PIN
#define FEATURE_SERVO 0
#define SERVO0_PIN 11
#define SERVO1_PIN -1
#define SERVO2_PIN -1
#define SERVO3_PIN -1
#define SERVO0_NEUTRAL_POS  -1
#define SERVO1_NEUTRAL_POS  -1
#define SERVO2_NEUTRAL_POS  -1
#define SERVO3_NEUTRAL_POS  -1
#define UI_SERVO_CONTROL 0
#define FAN_KICKSTART_TIME  200
        #define FEATURE_WATCHDOG 1
#define FEATURE_Z_PROBE 0
#define Z_PROBE_BED_DISTANCE 10
#define Z_PROBE_PIN -1
#define Z_PROBE_PULLUP 0
#define Z_PROBE_ON_HIGH 0
#define Z_PROBE_X_OFFSET 0
#define Z_PROBE_Y_OFFSET 0
#define Z_PROBE_WAIT_BEFORE_TEST 0
#define Z_PROBE_SPEED 2
#define Z_PROBE_XY_SPEED 150
#define Z_PROBE_SWITCHING_DISTANCE 1
#define Z_PROBE_REPETITIONS 1
#define Z_PROBE_HEIGHT 40
#define Z_PROBE_START_SCRIPT ""
#define Z_PROBE_FINISHED_SCRIPT ""
#define FEATURE_AUTOLEVEL 1
#define Z_PROBE_X1 20
#define Z_PROBE_Y1 20
#define Z_PROBE_X2 160
#define Z_PROBE_Y2 20
#define Z_PROBE_X3 100
#define Z_PROBE_Y3 160
#define FEATURE_AXISCOMP 0
#define AXISCOMP_TANXY 0
#define AXISCOMP_TANYZ 0
#define AXISCOMP_TANXZ 0
#define SDSUPPORT 1
#define SDCARDDETECT -1
#define SDCARDDETECTINVERTED 0
#define SD_EXTENDED_DIR 1
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

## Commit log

2018-08-23 Add designs of parts to print
    [Bisagra_lcd.stl, EjeX_Polea_rodamientoB623ZZ.stl, EjeX_carro_A.stl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]
2018-09-08 Continue organizing 3D printed parts
    [Bill of Materials.ods, Bisagra_lcd.stl, Configuration.h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]
2018-10-03 Add Gemstruder STL files
    [Gemstruder Big gear.stl, Gemstruder Idler.stl, Gemstruder Small gear.stl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]
2018-10-29 Add Gemstruder files v1.0
    [Gemstruder - Big Gear.stl, Gemstruder - Body.stl, Gemstruder - Idler Crossbar.stl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]

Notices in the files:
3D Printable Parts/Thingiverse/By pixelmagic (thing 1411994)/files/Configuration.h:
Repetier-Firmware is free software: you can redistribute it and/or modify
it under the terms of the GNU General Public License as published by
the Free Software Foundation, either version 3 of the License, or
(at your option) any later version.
